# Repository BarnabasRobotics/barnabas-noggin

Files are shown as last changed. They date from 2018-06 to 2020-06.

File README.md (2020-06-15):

# barnabas-noggin
Controller board for Barnabas-Bot.  Arduino-Uno compatible board.  

Versions:
 
 Using Nano plug-in board
 - V3: Rev 2C 
 - V3.1: Rev 2D, Rev 2E
 
 No nano plug-in board
 - V4: Rev 3A, 3B 

Changes in Rev2D:
 - Remove 5V regulator
 - Add fuse protection on 5V and 3.3V
 - Add DC Driver Controller
 - Fix silkscreen text

Changes in Rev2E:
 - Silkscreen updates

[AutoDesk Fusion 360 file](https://a360.co/3gs5b8a)

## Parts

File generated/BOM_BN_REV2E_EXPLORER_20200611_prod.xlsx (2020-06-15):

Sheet: Barnabas Noggin rev 2D
ITEM | PART ID | VALUE | PACKAGE | SPECIFICATION | QTY | NOTES | BRAND | DIGIKEY PART # | MFG PART # | Notes
1 | C1 | 1uF | 603 | C0603-ROUND | 1 |  | Yageo | 311-1445-2-ND | CC0603KRX5R8BB105 | Substitute is OK
2 | J5, J7, J8 | 2.54mm | Thru-Hole | 2.54 mm female 1 x 6 | 3 |  | Harwin Inc. | 952-1809-ND | M20-7820646 | Substitute is OK
3 | J6, J9 | 2.54mm | Thru-Hole | 2.54 mm female 1 x 8 | 2 |  | Sullins Connector Solutions | S7006-ND | PPTC081LFBN-RC | Substitute is OK
4 | C2, C3, C4, C5 | 100nF | 603 | C0603-ROUND | 4 |  | Yageo | 311-1343-2-ND | CC0603ZRY5V9BB104 | Substitute is OK
5 | R1, R2, E2 | 2.54mm | Thru-Hole | 1x 1 Pin Female Header | 6 | 1 pin per hole | PE Connectors | NA | HWS6903 | Substitute is OK
6 | Nano | 2.54mm | Thru-Hole | 2.54 mm female 1 x 15 | 2 |  | Sullins Connector Solutions | S7013-ND | ber PPTC151LFBN-RC | Substitute is OK
7 | F1, F2 | FUSE_6V | 603 | FUSE_0603 | 2 |  | Bourns Inc. | MF-FSMF050X-2CT-ND | MF-FSMF050X-2 | Substitute is OK
8 | J3, J4 | 2.54mm | Thru-Hole | 2.54 mm header 2 x 3 | 2 |  | Harwin Inc. | 952-2121-ND | M20-9980346 | Substitute is OK
9 | E1 | 2.54mm | Thru-Hole | 2.54 mm header 1 x 2 | 1 |  | PE Connectors | NA | hws5160 | Substitute is OK
10 | J1 | POWER_JACKPTH | Thru-Hole | POWER_JACK_PTH | 1 |  | MPD (Memory Protection Devices) | EJ508A-ND | EJ508A | Substitute is OK
11 | D1 | SS1P3L | DO-220AA | DIODI_DO220AAL | 1 |  | Vishay Semiconductor Diodes Division | SS1P3L-M3/84AGITR-ND | SS1P3L-M3/84A | Substitute is OK
 |  |  |  | Total Thru Hole | 17
 |  |  |  | Total SMD | 8
 |  |  |  | Total parts | 25

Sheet: Revision History
Date
2020-06-11 | Added LED header

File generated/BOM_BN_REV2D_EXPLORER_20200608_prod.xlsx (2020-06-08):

ITEM | PART ID | VALUE | PACKAGE | SPECIFICATION | QTY | NOTES | BRAND | DIGIKEY PART # | MFG PART # | Notes
1 | C1 | 1uF | 603 | C0603-ROUND | 1 |  | Yageo | 311-1445-2-ND | CC0603KRX5R8BB105
2 | J5, J7, J8 | 2.54mm | Thru-Hole | 2.54 mm female 1 x 6 | 3 |  | Harwin Inc. | 952-1809-ND | M20-7820646
3 | J6, J9 | 2.54mm | Thru-Hole | 2.54 mm female 1 x 8 | 2 |  | Sullins Connector Solutions | S7006-ND | PPTC081LFBN-RC
5 | C2, C3, C4, C5 | 100nF | 603 | C0603-ROUND | 4 |  | Yageo | 311-1343-2-ND | CC0603ZRY5V9BB104
6 | R1, R2 | 470 | Thru-Hole | RESISTOR_PTH | 2 | NO PLACE | * | * | * | NO PLACE
7 | Nano | 2.54mm | Thru-Hole | 2.54 mm female 1 x 15 | 2 |  | Sullins Connector Solutions | S7013-ND | ber PPTC151LFBN-RC
8 | E2 | BUZZER | Thru-Hole | 5V Passive buzzer | 1 | NO PLACE | * | * | * | NO PLACE
9 | F1, F2 | FUSE_6V | 603 | FUSE_0603 | 2 |  | Bourns Inc. | MF-FSMF050X-2CT-ND | MF-FSMF050X-2
10 | J3, J4 | 2.54mm | Thru-Hole | 2.54 mm header 2 x 3 | 2 |  | Harwin Inc. | 952-2121-ND | M20-9980346
11 | E1 | 5mm | Thru-Hole | LED5MM | 1 | NO PLACE | * | * | * | NO PLACE
12 | J1 | POWER_JACKPTH | Thru-Hole | POWER_JACK_PTH | 1 |  | MPD (Memory Protection Devices) | EJ508A-ND | EJ508A
13 | D1 | SS1P3L | DO-220AA | DIODI_DO220AAL | 1 |  | Vishay Semiconductor Diodes Division | SS1P3L-M3/84AGITR-ND | SS1P3L-M3/84A
 |  |  |  | Total Thru Hole | 14
 |  |  |  | Total SMD | 8
 |  |  |  | Total parts | 22

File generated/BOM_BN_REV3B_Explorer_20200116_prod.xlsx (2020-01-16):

ITEM | PART ID | VALUE | PACKAGE | SPECIFICATION | QTY | NOTES | BRAND | DIGIKEY PART # | MFG PART # | Notes
1 | R1, R4, R5, R6, R7, R8, R9 | 1K | 603 | RES SMD 1K OHM 1% 1/10W 0603 | 7 |  | Yageo | 311-1.00KHRTR-ND | RC0603FR-071KL
2 | C2, C4, C5, C6, C13 | 1uF | 603 | CAP CER 1UF 25V X5R 0603 | 5 |  | Yageo | 311-1445-2-ND | CC0603KRX5R8BB105
3 | J6, J7, J9 | 2.54mm | Thru-Hole | CONN RCPT 6POS 0.1 TIN PCB | 3 |  | Harwin Inc. | 952-1809-ND | M20-7820646
4 | J8, J10 | 2.54mm | Thru-Hole | CONN HDR 8POS 0.1 TIN PCB | 2 |  | Sullins Connector Solutions | S7006-ND | PPTC081LFBN-RC
5 | R2 | 4.7K | Thru-Hole | Thru-Hole Resistor | 1 | No Place | * | * | * | No Place
6 | C3, C10 | 4.7uF | 1206 | CAP CER 4.7UF 16V X5R 1206 | 2 |  | Samsung Electro-Mechanics | 1276-3059-2-ND | CL31A475KOHNNNE
7 | X2 | 12MHz | 3-SMD | CER RES 12.0000MHZ 33PF SMD | 1 |  | Murata Electronics North America | 490-17943-2-ND | CSTNE12M0G550000R0
8 | X1 | 16MHZ | 3-SMD | CER RES 16.0000MHZ 15PF SMD | 1 |  | Murata Electronics North America | 490-17948-2-ND | CSTNE16M0V530000R0
9 | C1, C7, C8, C9, C11, C12, C14, C15 | 100nF | 603 | CAP CER 0.1UF 50V Y5V 0603 | 8 |  | Yageo | 311-1343-2-ND | CC0603ZRY5V9BB104
10 | PB1, PB2 | 157SW | * | SWITCH TACTILE SPST-NO 0.05A 12V | 2 |  | C&K | CKN10506TR-ND | PTS820 J15M SMTR LFS
11 | R3 | 470 | Thru-Hole | Thru-Hole Resistor | 1 | No Place | * | * | * | No Place
12 | U2 | ATMEGA328P-AU | TQFP32-08 | IC MCU 8BIT 32KB FLASH 32TQFP | 1 |  | Microchip Technology | ATMEGA328P-AU-ND | ATMEGA328P-AU
13 | E2 | BUZZER | Thru-Hole | 5V Passive Buzzer | 1 | No Place | * | * | * | No Place
14 | U4 | CH340G | * | CH340G | 1 |  | * | * | *
15 | F1, F2, F3 | FUSE_6V | 603 | PTC RESET FUSE 6V 500MA 0603 | 3 |  | Bourns Inc. | MF-FSMF050X-2CT-ND | MF-FSMF050X-2
16 | LED1, LED4 | Green | 805 | LED GREEN CLEAR CHIP SMD | 2 |  | Lite-On Inc. | 160-1423-2-ND | LTST-C171GKT
17 | J2, J3, J5 | ICSP | Thru-Hole | CONN HEADER VERT 6POS 2.54MM | 3 |  | Harwin Inc. | 952-2121-ND | M20-9980346
18 | U5 | L9110S_DRIVER | * | DC Motor Driver | 1 | No Place | * | * | * | No Place
19 | E1 | LEDPTH | Thru-Hole | Thru-Hole 3V LED | 1 | No Place | * | * | * | No Place
20 | U1 | LM1117IMPX-5.0 | SOT-223-4 | IC REG LINEAR 5V 800MA SOT223-4 | 1 |  | Texas Instruments | LM1117IMPX-5.0/NOPBTR-ND | LM1117IMPX-5.0/NOPB
21 | U3 | LP2985-XXDBVR | SOT-23-5 | IC REG LINEAR 3.3V 150MA SOT23-5 | 1 |  | Texas Instruments | 296-18476-2-ND | LP2985-33DBVR
22 | J1 | POWER_JACKPTH | Thru-Hole | CONN PWR JACK 2.1X5.5MM SOLDER | 1 |  | MPD (Memory Protection Devices) | EJ508A-ND | EJ508A
23 | LED3 | Red | 805 | LED RED CLEAR SMD | 1 |  | Lite-On Inc. | 160-1415-2-ND | LTST-C170KRKT
24 | D1, D2, D3 | SS1P3L | DO-220AA | DIODE SCHOTTKY 30V 1.5A DO220AA | 3 |  | Vishay Semiconductor Diodes Division | SS1P3L-M3/84AGITR-ND | SS1P3L-M3/84A
25 | J4 | USB-mini-90 -SMD | * | CONN RCPT USB2.0 MINI B SMD R/A | 1 |  | CUI Inc. | 102-4003-2-ND | UJ2-MBH-1-SMT-TR
26 | LED2 | Yellow | 805 | LED YELLOW CLEAR CHIP SMD | 1 |  | Lite-On Inc. | 160-1428-2-ND | LTST-C171KSKT
 | Total Thru Hole | 13
 | Total SMD | 42
 | Total Parts | 55

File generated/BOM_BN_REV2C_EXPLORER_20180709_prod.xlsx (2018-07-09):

ITEM | PART ID | VALUE | PACKAGE | SPECIFICATION | QTY | NOTES | BRAND | DIGIKEY PART # | MFG PART # | Notes | EBAY LINK
1 | BUZZER7 | 5V | Thru-Hole (12 mm) | 5V Active buzzer | 0 | NO PLACE |  |  |  | NO PLACE
2 | C1, C2, C3, C4, C5, C6 | 100 nF | 1206 | 100 nF SMD | 6 |  | Kemet | 399-1249-2-ND | C1206C104K5RAC7867 |  | http://www.ebay.com/itm/291539757911
3 | D1 | 1A 400V | Thru-Hole (DO41-10) | 1N4004 Diode | 1 |  | Diodes Incorporated | 1N4004DITR-ND | 1N4004-T |  | http://www.ebay.com/itm/141976942383
4 | VR1 | 5V | SOT223 | AMS1117-5.0 | 0 | NO PLACE | Advanced Monolithic Systems |  | AMS1117-5.0 |  | http://www.ebay.com/itm/361426721949
5 | 7-12V | NA | Thru-Hole | 2.1 mm DC connector | 1 |  | MPD (Memory Protection Devices) | EJ508A-ND | EJ508A |  | http://www.ebay.com/itm/261471107446
6 | 01234567, 8910111213GNDREF | 2.54mm | Thru-Hole | 2.54 mm female 1 x 8 | 2 |  | Sullins Connector Solutions | S7006-ND | PPTC081LFBN-RC |  | http://www.ebay.com/itm/171015694191
7 | VINGNDGND5V3.3VRST, A5A4A3A2A1A0 | 2.54mm | Thru-Hole | 2.54 mm female 1 x 6 | 2 |  | Harwin Inc. | 952-1809-ND | M20-7820646 |  | http://www.ebay.com/itm/171015694317
8 | SERVO3SERVO9, SERVO10SERVO11 | 2.54mm | Thru-Hole | 2.54 mm header 2 x 3 | 2 |  | Harwin Inc. | 952-2121-ND | M20-9980346 |  | http://www.ebay.com/itm/500pc-Gold-plated-Double-Rows-2x3-pins-2-54mm-H-11-6mm-Male-Pin-Header-RoHS-/130544119410
9 | LED7 | 5mm | Thru-Hole | 3V LED 5mm diameter | 0 | NO PLACE |  |  |  | NO PLACE
10 | R1, R2 | 470 Ohm | Thru-Hole | Resistor | 0 | NO PLACE |  |  |  | NO PLACE
11 | NANO | 2.54mm | Thru-Hole | 2.54 mm female 1 x 15 | 2 |  | Sullins Connector Solutions | S7013-ND | ber PPTC151LFBN-RC
 |  |  |  | Total Thru Hole | 10
 |  |  |  | Total SMD | 6
 |  |  |  | Total parts | 16

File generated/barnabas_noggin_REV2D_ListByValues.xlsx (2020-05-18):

Qty | Value | Part Num | Package | Parts | Mfg Name | VID | Vendor Part Num | Description | Pkg Code | XREF
1 | 1uF | CC0603KRX5R8BB105 | C0603-ROUND | C1 | Yageo | DK | 311-1445-2-ND | CAP CER 1UF 25V X5R 0603 | 603 | REF9
3 | 2.54mm | M20-7820646 | 1X06 | J5, J7, J8 | Harwin Inc. | DK | 952-1809-ND | CONN RCPT 6POS 0.1 TIN PCB | REF19 | *
2 | 2.54mm | PPTC081LFBN-RC | 1X08 | J6, J9 | Sullins Connector Solutions | DK | S7006-ND | CONN HDR 8POS 0.1 TIN PCB | REF18 | *
1 | 4.7K | * | RESISTOR_PTH | R1 | * | * | * | * | * | *
4 | 100nF | CC0603ZRY5V9BB104 | C0603-ROUND | C2, C3, C4, C5 | Yageo | DK | 311-1343-2-ND | CAP CER 0.1UF 50V Y5V 0603 | 603 | REF10
1 | 470 | * | RESISTOR_PTH | R2 | * | * | * | * | * | *
1 | ARDUINONANO | * | PDIP-32 | U$1 | * | * | * | * | * | *
1 | BUZZER | * | BUZZER | E2 | * | * | * | * | * | *
2 | FUSE_6V | MF-FSMF050X-2 | FUSE_0603 | F1, F2 | Bourns Inc. | DK | MF-FSMF050X-2CT-ND | PTC RESET FUSE 6V 500MA 0603 | 603 | REF1
2 | ICSP | M20-9980346 | CONNECTOR_2X3 | J3, J4 | Harwin Inc. | DK | 952-2121-ND | CONN HEADER VERT 6POS 2.54MM | * | REF20
1 | L9110S_DRIVER | * | L9110S_DRIVER | U1 | * | * | * | * | * | *
1 | LEDPTH | * | LED5MM | E1 | * | * | * | * | * | *
1 | POWER_JACKPTH | EJ508A | POWER_JACK_PTH | J1 | MPD (Memory Protection Devices) | DK | EJ508A-ND | CONN PWR JACK 2.1X5.5MM SOLDER | * | REF17
1 | SS1P3L | SS1P3L-M3/84A | DIODI_DO220AAL | D1 | Vishay Semiconductor Diodes Division | DK | SS1P3L-M3/84AGITR-ND | DIODE SCHOTTKY 30V 1.5A DO220AA | DO-220AA | REF5

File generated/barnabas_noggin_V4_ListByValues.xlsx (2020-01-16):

Qty | Value | Part Num | Package | Parts | Mfg Name | VID | Vendor Part Num | Description | Pkg Code | XREF
7 | 1K | RC0603FR-071KL | R0603 | R1, R4, R5, R6, R7, R8, R9 | Yageo | DK | 311-1.00KHRTR-ND | RES SMD 1K OHM 1% 1/10W 0603 | 603 | REF7
5 | 1uF | CC0603KRX5R8BB105 | C0603-ROUND | C2, C4, C5, C6, C13 | Yageo | DK | 311-1445-2-ND | CAP CER 1UF 25V X5R 0603 | 603 | REF9
3 | 2.54mm | M20-7820646 | 1X06 | J6, J7, J9 | Harwin Inc. | DK | 952-1809-ND | CONN RCPT 6POS 0.1 TIN PCB | REF19 | *
2 | 2.54mm | PPTC081LFBN-RC | 1X08 | J8, J10 | Sullins Connector Solutions | DK | S7006-ND | CONN HDR 8POS 0.1 TIN PCB | REF18 | *
1 | 4.7K | * | RESISTOR_PTH | R2 | * | * | * | * | * | *
2 | 4.7uF | CL31A475KOHNNNE | TAN-A | C3, C10 | Samsung Electro-Mechanics | DK | 1276-3059-2-ND | CAP CER 4.7UF 16V X5R 1206 | 1206 | REF11
1 | 12MHz | CSTNE12M0G550000R0 | CRYSTAL | X2 | Murata Electronics North America | DK | 490-17943-2-ND | CER RES 12.0000MHZ 33PF SMD | 3-SMD | REF4
1 | 16MHZ | CSTNE16M0V530000R0 | CRYSTAL | X1 | Murata Electronics North America | DK | 490-17948-2-ND | CER RES 16.0000MHZ 15PF SMD | 3-SMD | REF3
8 | 100nF | CC0603ZRY5V9BB104 | C0603-ROUND | C1, C7, C8, C9, C11, C12, C14, C15 | Yageo | DK | 311-1343-2-ND | CAP CER 0.1UF 50V Y5V 0603 | 603 | REF10
2 | 157SW | PTS820 J15M SMTR LFS | SWITCHES_SMD_157SW | PB1, PB2 | C&K | DK | CKN10506TR-ND | SWITCH TACTILE SPST-NO 0.05A 12V | REF23 | *
1 | 470 | * | RESISTOR_PTH | R3 | * | * | * | * | * | *
1 | ATMEGA328P-AU | ATMEGA328P-AU | TQFP32-08 | U2 | Microchip Technology | DK | ATMEGA328P-AU-ND | IC MCU 8BIT 32KB FLASH 32TQFP | 32-TQFP | REF2
1 | BUZZER | * | BUZZER | E2 | * | * | * | * | * | *
1 | CH340G | * | SOIC16 | U4 | * | * | * | * | * | *
3 | FUSE_6V | MF-FSMF050X-2 | FUSE_0603 | F1, F2, F3 | Bourns Inc. | DK | MF-FSMF050X-2CT-ND | PTC RESET FUSE 6V 500MA 0603 | 603 | REF1
2 | Green | LTST-C171GKT | LED_0805 | LED1, LED4 | Lite-On Inc. | DK | 160-1423-2-ND | LED GREEN CLEAR CHIP SMD | 805 | REF12
3 | ICSP | M20-9980346 | CONNECTOR_2X3 | J2, J3, J5 | Harwin Inc. | DK | 952-2121-ND | CONN HEADER VERT 6POS 2.54MM | * | REF20
1 | L9110S_DRIVER | * | L9110S_DRIVER | U5 | * | * | * | * | * | *
1 | LEDPTH | * | LED5MM | E1 | * | * | * | * | * | *
1 | LM1117IMPX-5.0 | LM1117IMPX-5.0/NOPB | LM1117_SOT223 | U1 | Texas Instruments | DK | LM1117IMPX-5.0/NOPBTR-ND | IC REG LINEAR 5V 800MA SOT223-4 | SOT-223-4 | REF6
1 | LP2985-XXDBVR | LP2985-33DBVR | SOT23-DBV | U3 | Texas Instruments | DK | 296-18476-2-ND | IC REG LINEAR 3.3V 150MA SOT23-5 | SOT-23-5 | REF22
4 | MOUNT_HOLE | * | MOUNT_HOLE | M1, M2, M3, M4 | * | * | * | * | * | *
1 | POWER_JACKPTH | EJ508A | POWER_JACK_PTH | J1 | MPD (Memory Protection Devices) | DK | EJ508A-ND | CONN PWR JACK 2.1X5.5MM SOLDER | * | REF17
1 | Red | LTST-C170KRKT | LED_0805 | LED3 | Lite-On Inc. | DK | 160-1415-2-ND | LED RED CLEAR SMD | 805 | REF13
3 | SS1P3L | SS1P3L-M3/84A | DIODI_DO220AAL | D1, D2, D3 | Vishay Semiconductor Diodes Division | DK | SS1P3L-M3/84AGITR-ND | DIODE SCHOTTKY 30V 1.5A DO220AA | DO-220AA | REF5
1 | USB-mini-90 -SMD | UJ2-MBH-1-SMT-TR | CONNECTOR_USB_MINI-B | J4 | CUI Inc. | DK | 102-4003-2-ND | CONN RCPT USB2.0 MINI B SMD R/A | * | REF21
1 | Yellow | LTST-C171KSKT | LED_0805 | LED2 | Lite-On Inc. | DK | 160-1428-2-ND | LED YELLOW CLEAR CHIP SMD | 805 | REF14

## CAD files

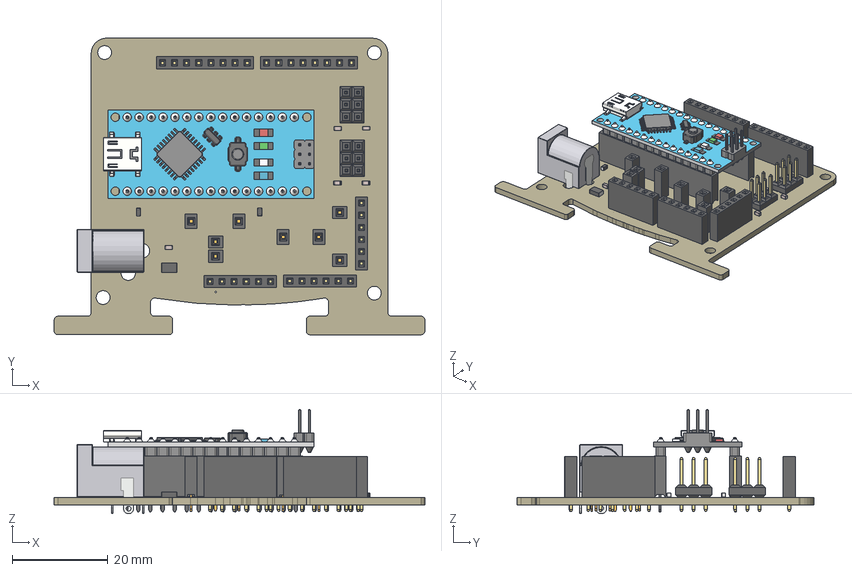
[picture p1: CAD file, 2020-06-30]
generated/barnabas_noggin_Rev2E.step
77.7 x 62.1 x 21.9 mm
1X06 x 3
1X08 x 2
C0603-ROUND x 5
CONNECTOR_2X3 x 2
DIODI_DO220AAL
FUSE_0603 x 2
L9110S_DRIVER
POWER_JACK_PTH
arduio nano
ZL262-1S_P2-54_L2-54_W2-54_H8-5 x 2
ZL262-1S_P2-54_L2-54_W2-54_H8-5 (1) x 2
ZL262-1S_P2-54_L2-54_W2-54_H8-5 (2) x 4

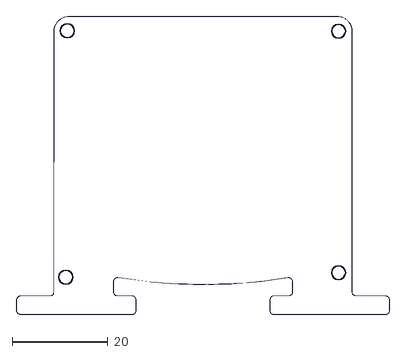
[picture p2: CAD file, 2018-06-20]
pcb-outline/schematic_V3_mm_2_r14 version.dxf
77.8 x 62.2

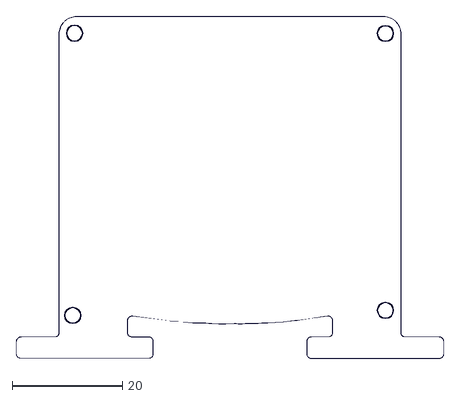
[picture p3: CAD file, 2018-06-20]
pcb-outline/schematic_V3_mm.dxf
77.8 x 62.2

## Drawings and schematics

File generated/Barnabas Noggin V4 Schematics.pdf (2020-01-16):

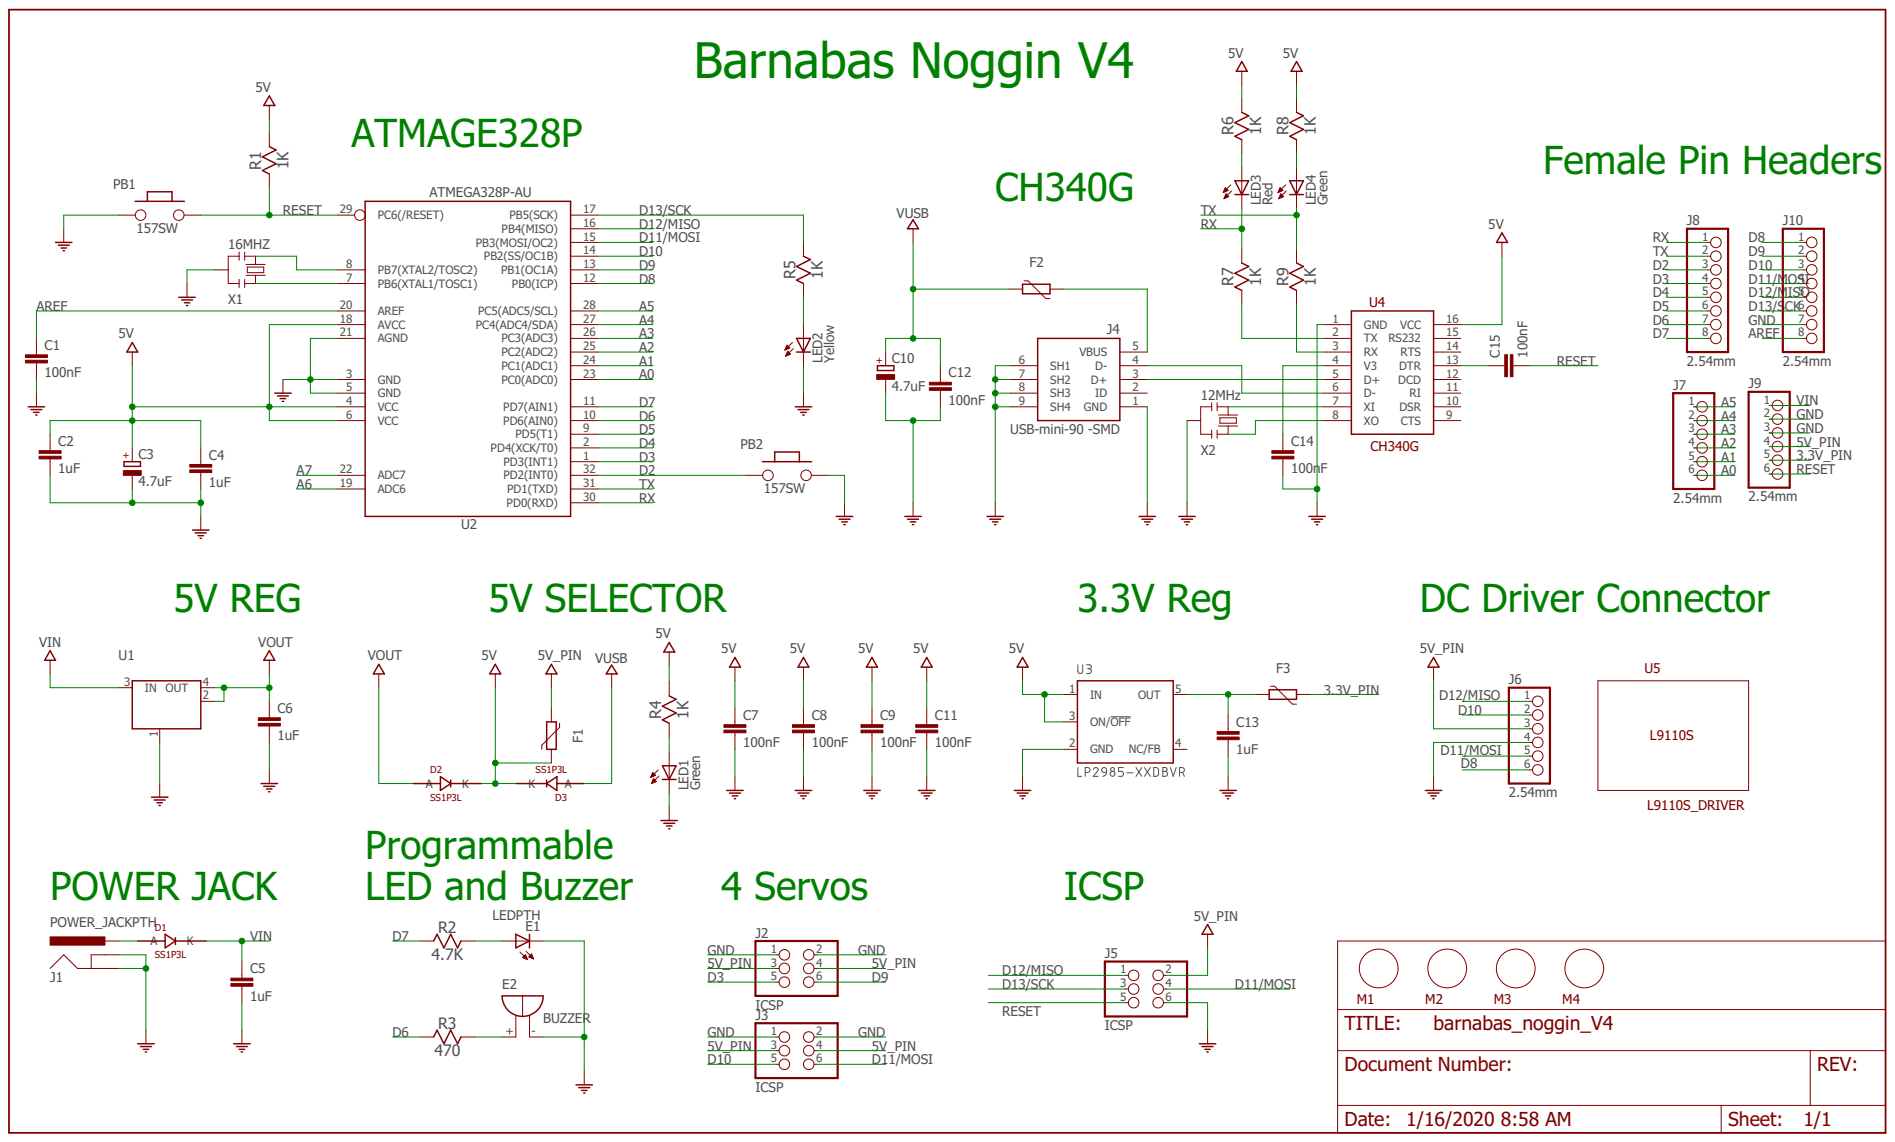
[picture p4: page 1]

REV: TITLE: Document Number: barnabas_noggin_V4

Date: 1/16/2020 8:58 AM | Sheet: 1/1

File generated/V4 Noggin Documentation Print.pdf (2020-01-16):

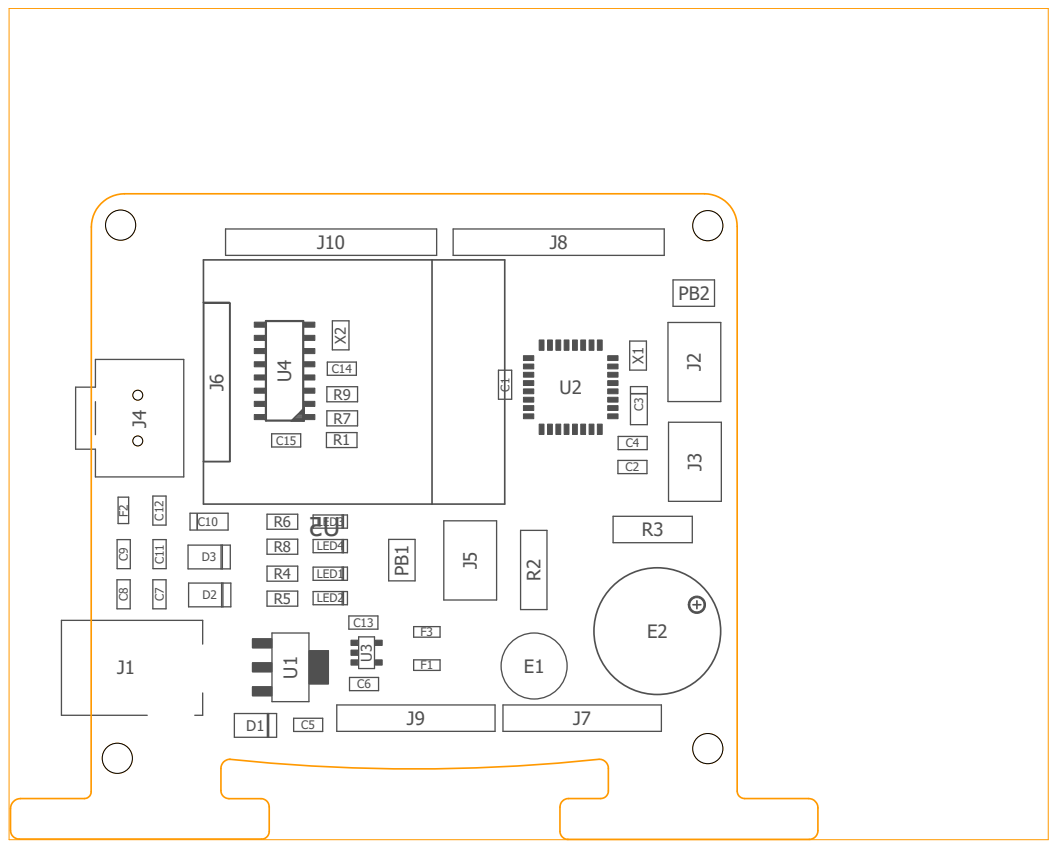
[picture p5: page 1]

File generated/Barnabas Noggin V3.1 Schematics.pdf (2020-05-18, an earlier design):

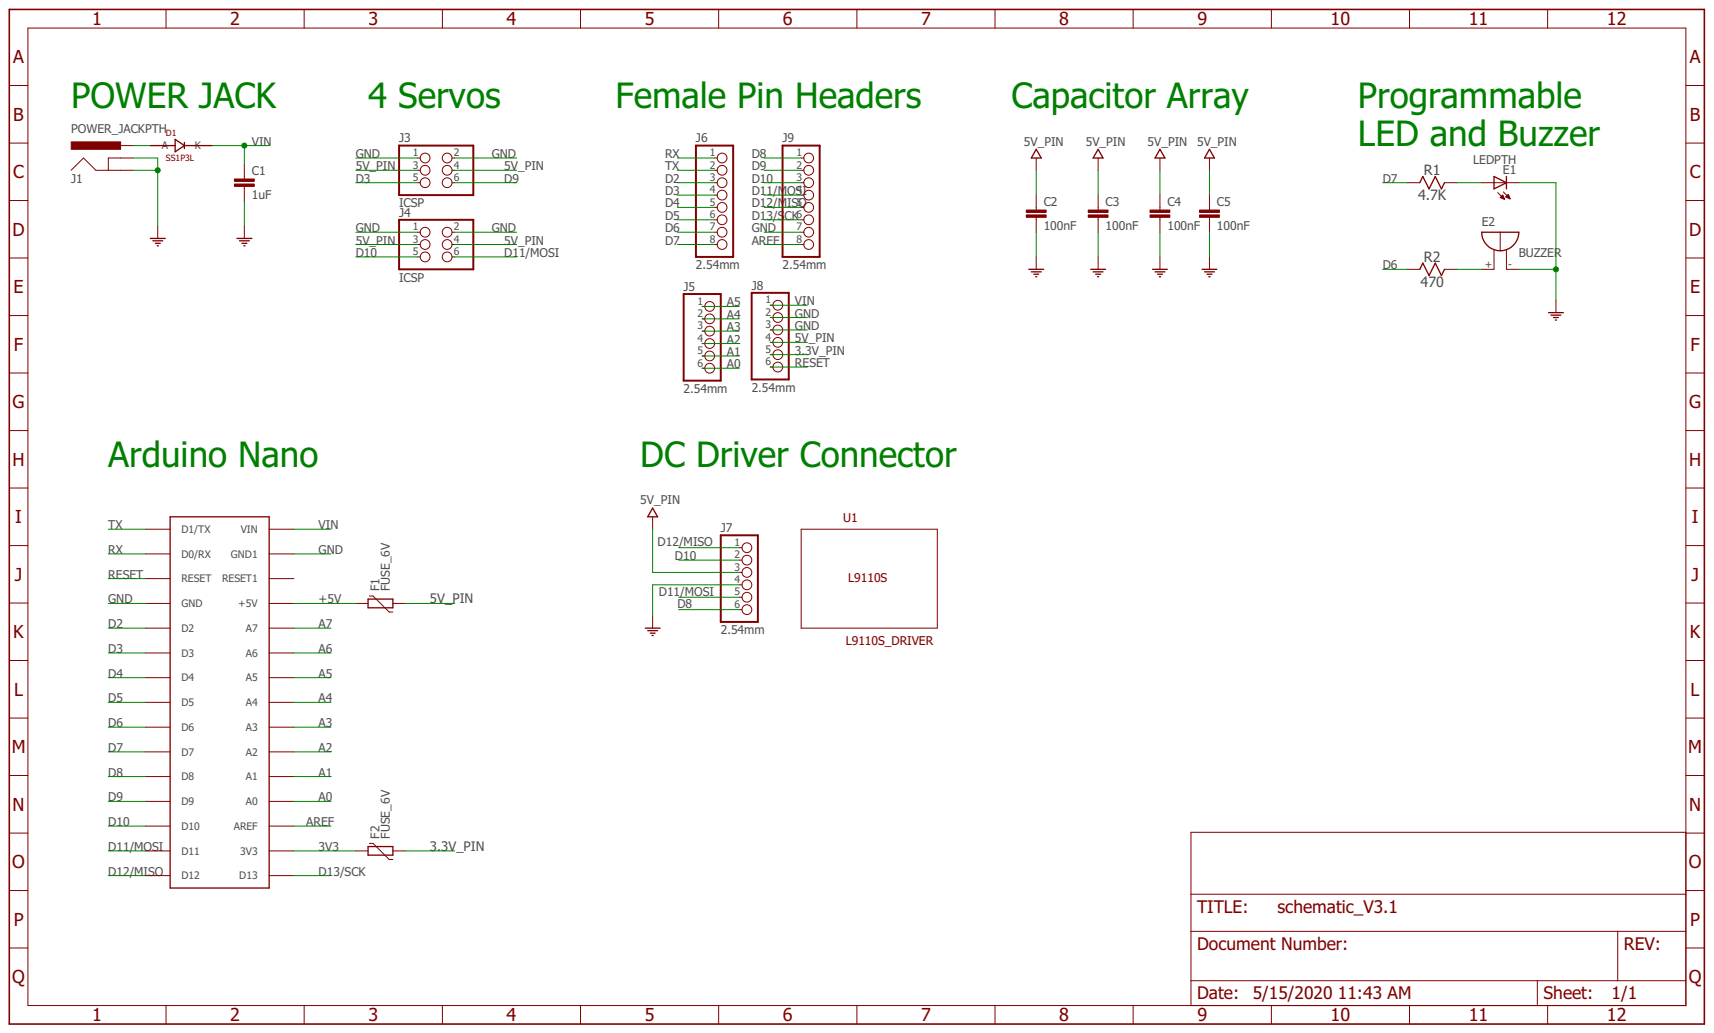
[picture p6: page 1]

REV: TITLE: Document Number: schematic_V3.1

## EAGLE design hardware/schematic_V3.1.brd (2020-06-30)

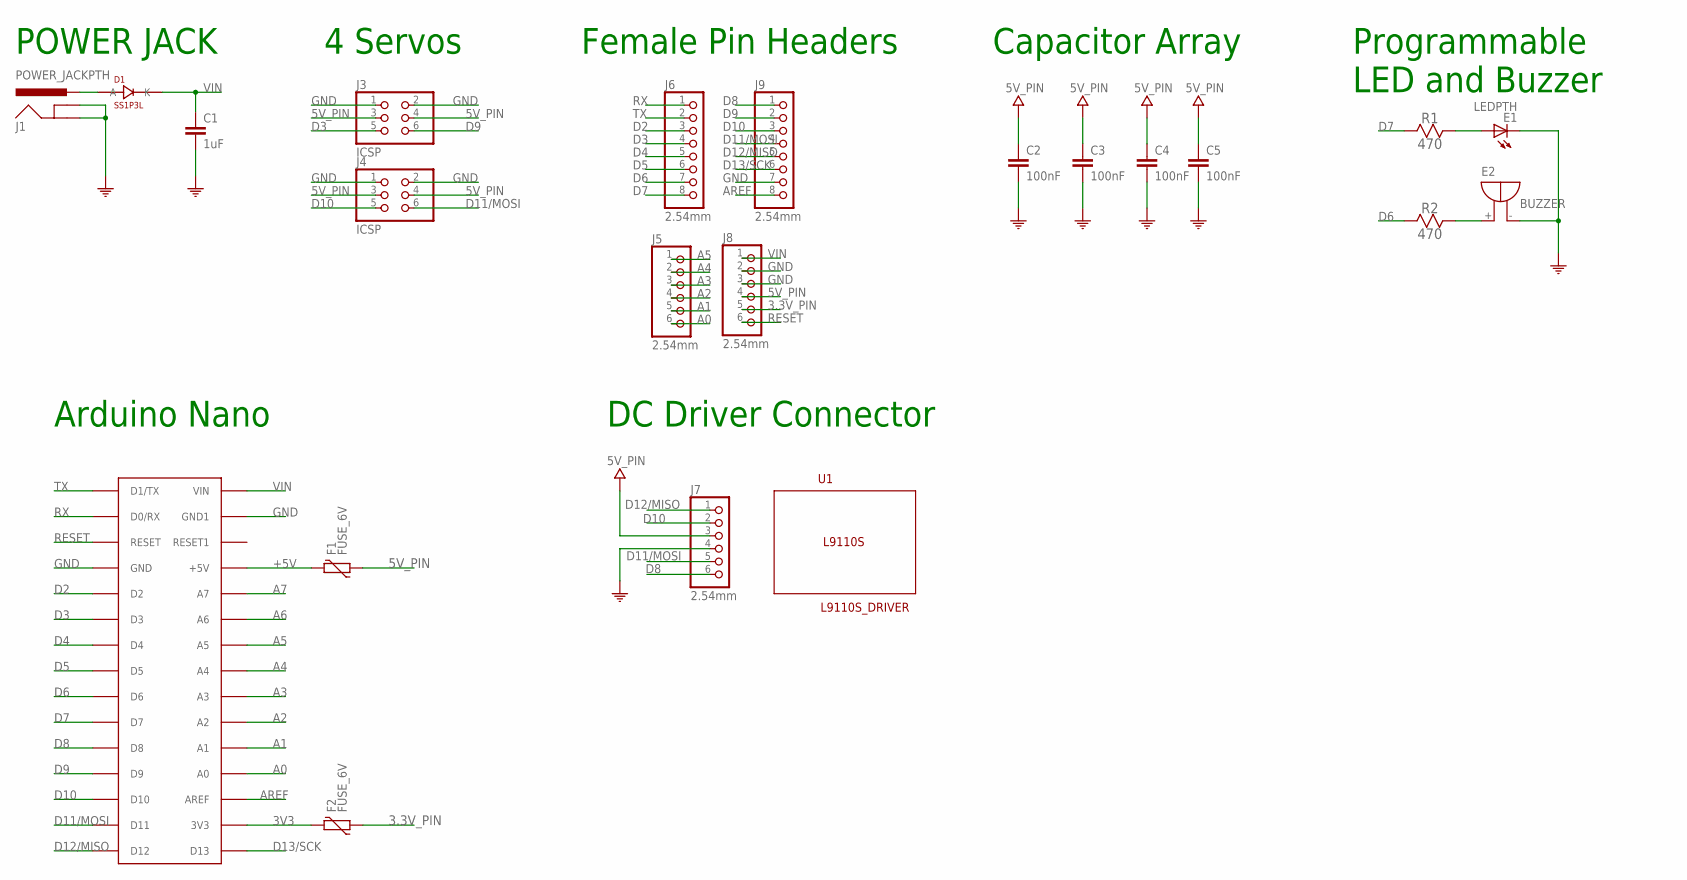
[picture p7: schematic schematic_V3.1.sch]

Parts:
C1: 1uF; C0603-ROUND; PARTNO CC0603KRX5R8BB105
C2, C3, C4, C5: 100nF; C0603-ROUND; PARTNO CC0603ZRY5V9BB104
D1: SS1P3L; DIODI_DO220AAL; PARTNO SS1P3L-M3/84A
E1: LEDPTH; LED5MM
E2: BUZZER
F1, F2: FUSE_6V; FUSE_0603; PARTNO MF-FSMF050X-2
J1: POWER_JACKPTH; POWER_JACK_PTH; PARTNO EJ508A
J3, J4: ICSP; CONNECTOR_2X3; PARTNO M20-9980346
J5, J7, J8: 2.54mm; 1X06; PARTNO M20-7820646
J6, J9: 2.54mm; 1X08; PARTNO PPTC081LFBN-RC
R1, R2: 470; RESISTOR_PTH
U1: L9110S_DRIVER
U$1: ARDUINONANO; PDIP-32

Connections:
3.3V_PIN: F2.1, J8.5
3V3: F2.2, U$1.3V3
5V_PIN: C2.1, C3.1, C4.1, C5.1, F1.1, J3.3, J3.4, J4.3, J4.4, J7.3, J8.4
+5V: F1.2, U$1.+5V
A0: J5.6, U$1.A7 (A0)
A1: J5.5, U$1.A6 (A1)
A2: J5.4, U$1.A5 (A2)
A3: J5.3, U$1.A4 (A3)
A4: J5.2, U$1.A3 (A4)
A5: J5.1, U$1.A2 (A5)
A6: U$1.A1 (A6)
A7: U$1.A0 (A7)
AREF: J9.8, U$1.AREF
D2: J6.3, U$1.D2
D3: J3.5, J6.4, U$1.D3
D4: J6.5, U$1.D4
D5: J6.6, U$1.D5
D6: J6.7, R2.1, U$1.D6
D7: J6.8, R1.1, U$1.D7
D8: J7.6, J9.1, U$1.D8
D9: J3.6, J9.2, U$1.D9
D10: J4.5, J7.2, J9.3, U$1.D10
D11/MOSI: J4.6, J7.5, J9.4, U$1.D11
D12/MISO: J7.1, J9.5, U$1.D12
D13/SCK: J9.6, U$1.D13
GND: C1.2, C2.2, C3.2, C4.2, C5.2, E1.K (C), E2.-, J1.GND, J1.GNDBREAK, J3.1, J3.2, J4.1, J4.2, J7.4, J8.2, J8.3, J9.7, U$1.GND, U$1.GND1
unnamed: D1.P$2 (A), J1.PWR
unnamed: E1.A, R1.2
unnamed: E2.+, R2.2
RESET: J8.6, U$1.RESET
RX: J6.1, U$1.D0/RX
TX: J6.2, U$1.D1/TX
VIN: C1.1, D1.P$1 (K), J8.1, U$1.VIN

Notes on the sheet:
Arduino Nano
POWER JACK
4 Servos
Female Pin Headers
Programmable LED and Buzzer
Capacitor Array
DC Driver Connector

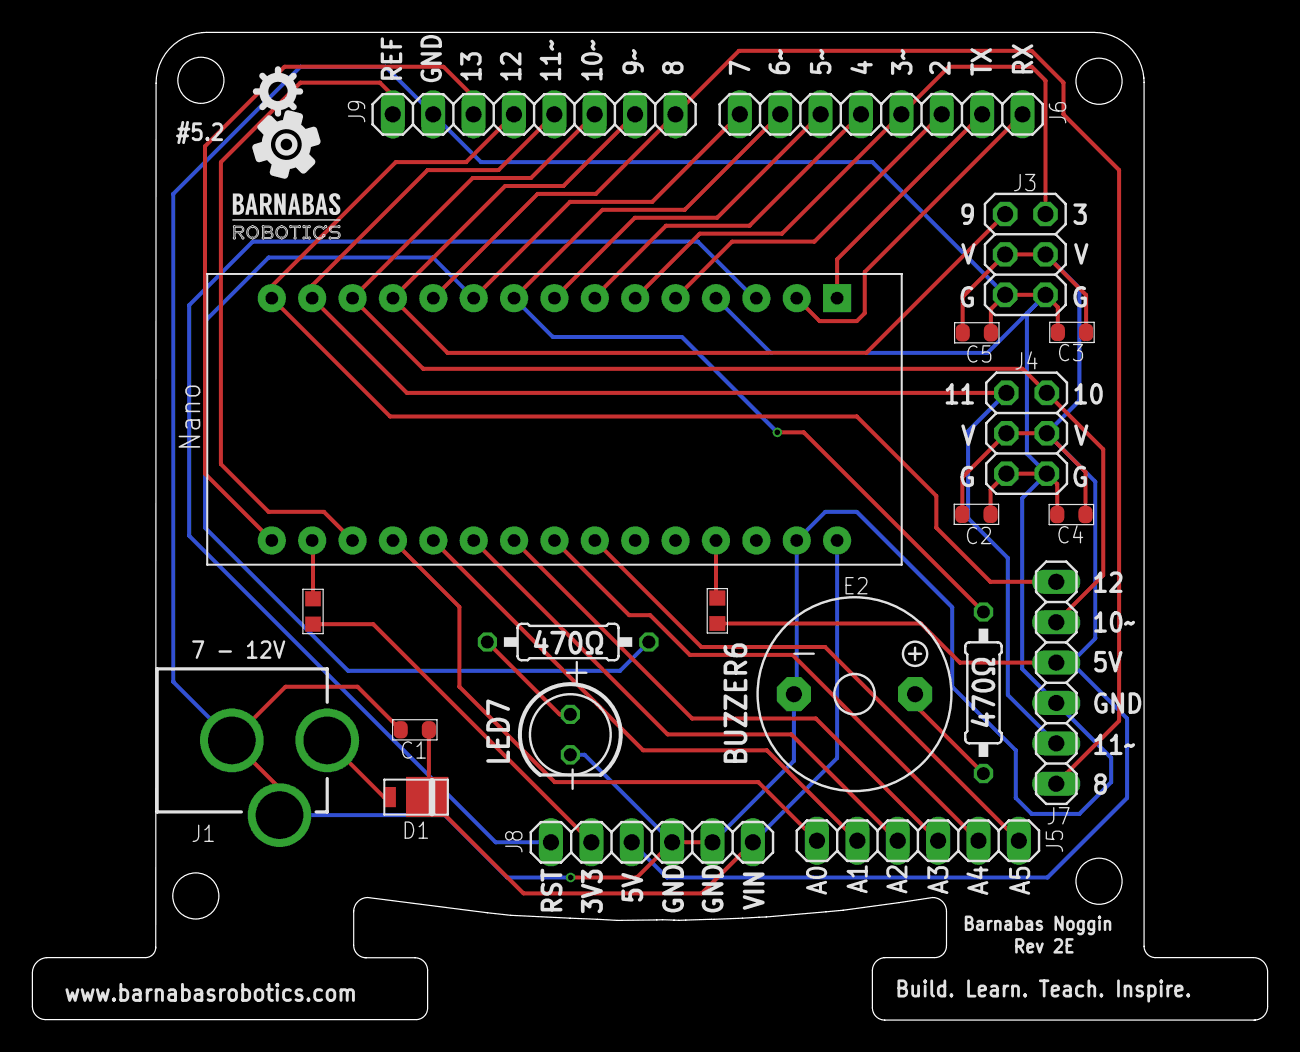
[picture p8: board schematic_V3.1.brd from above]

Board: 2 copper layers, 77.7 x 62.1 mm, 22 parts (0 on the bottom side), 31 nets.

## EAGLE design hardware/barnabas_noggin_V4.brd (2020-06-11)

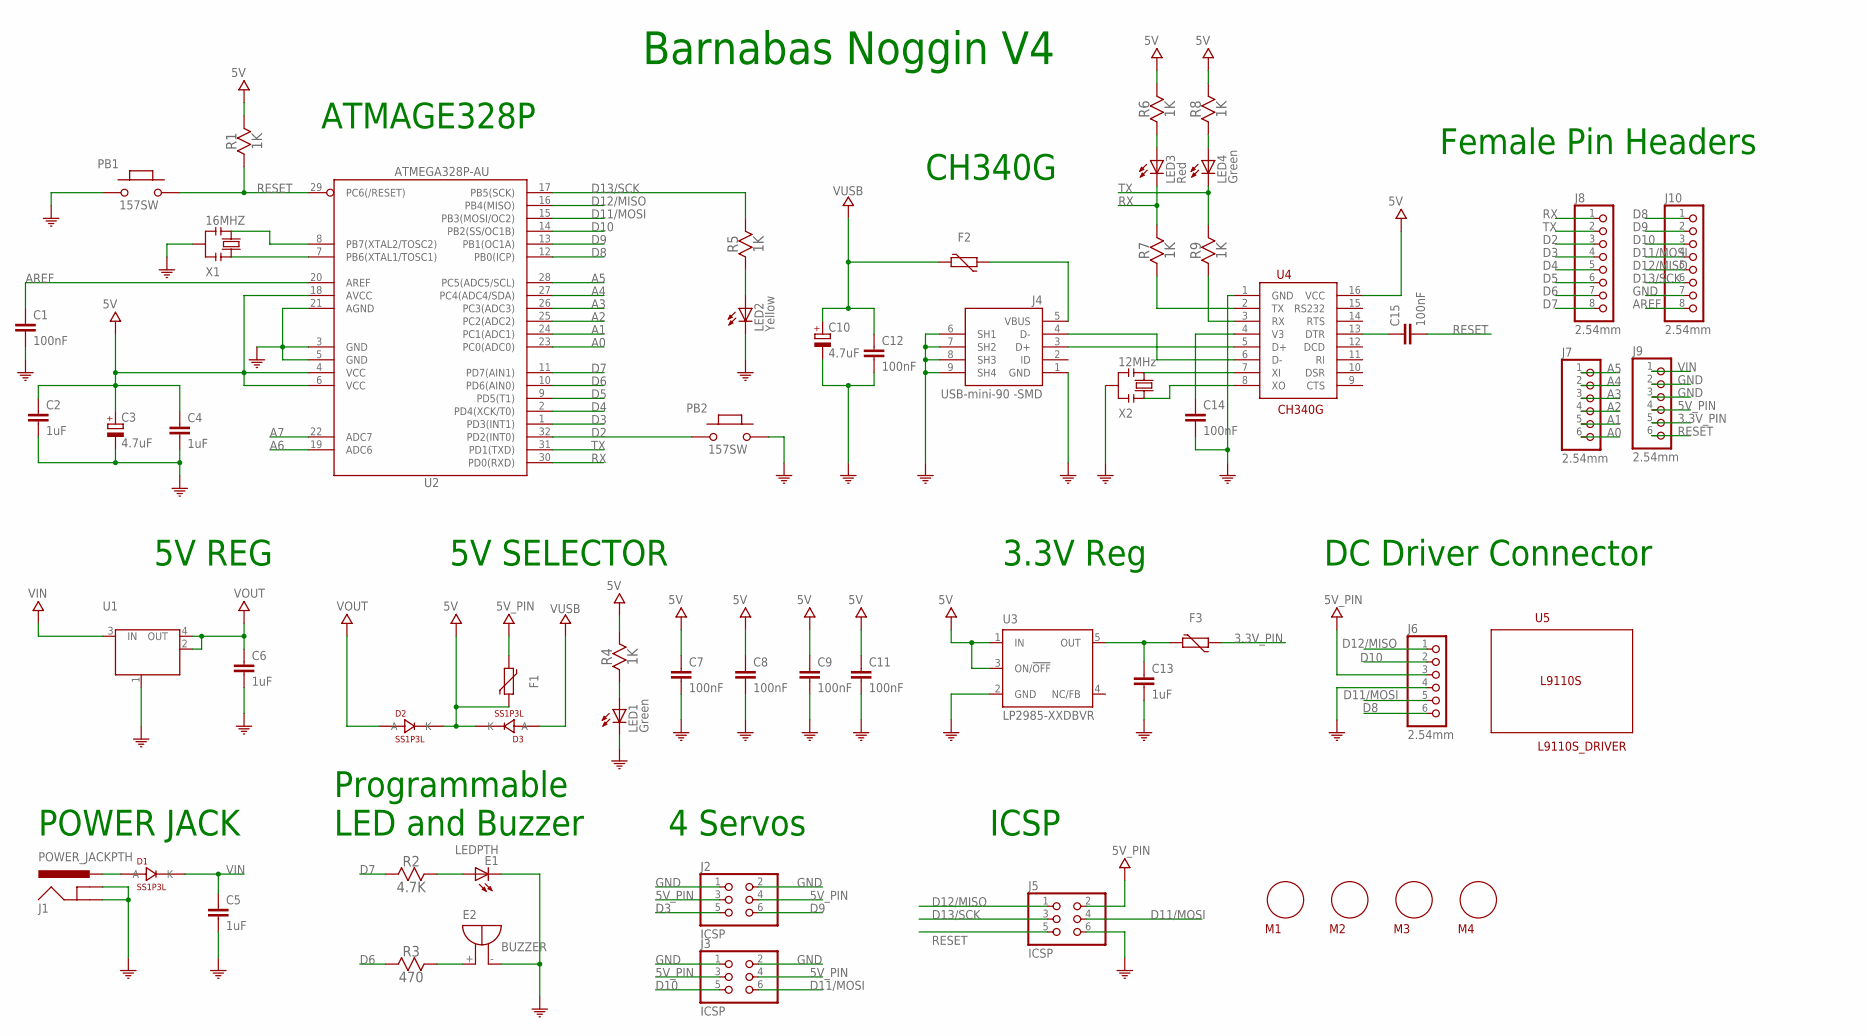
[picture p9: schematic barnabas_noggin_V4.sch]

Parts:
C1, C7, C8, C9, C11, C12, C14, C15: 100nF; C0603-ROUND; PARTNO CC0603ZRY5V9BB104
C2, C4, C5, C6, C13: 1uF; C0603-ROUND; PARTNO CC0603KRX5R8BB105
C3, C10: 4.7uF; TAN-A; PARTNO CL31A475KOHNNNE
D1, D2, D3: SS1P3L; DIODI_DO220AAL; PARTNO SS1P3L-M3/84A
E1: LEDPTH; LED5MM
E2: BUZZER
F1, F2, F3: FUSE_6V; FUSE_0603; PARTNO MF-FSMF050X-2
J1: POWER_JACKPTH; POWER_JACK_PTH; PARTNO EJ508A
J2, J3, J5: ICSP; CONNECTOR_2X3; PARTNO M20-9980346
J4: USB-mini-90 -SMD; CONNECTOR_USB_MINI-B; PARTNO UJ2-MBH-1-SMT-TR
J6, J7, J9: 2.54mm; 1X06; PARTNO M20-7820646
J8, J10: 2.54mm; 1X08; PARTNO PPTC081LFBN-RC
LED1, LED4: Green; LED_0805; PARTNO LTST-C171GKT
LED2: Yellow; LED_0805; PARTNO LTST-C171KSKT
LED3: Red; LED_0805; PARTNO LTST-C170KRKT
M1, M2, M3, M4: MOUNT_HOLE
PB1, PB2: 157SW; SWITCHES_SMD_157SW; PARTNO PTS820 J15M SMTR LFS
R1, R4, R5, R6, R7, R8, R9: 1K; R0603; PARTNO RC0603FR-071KL
R2: 4.7K; RESISTOR_PTH
R3: 470; RESISTOR_PTH
U1: LM1117IMPX-5.0; LM1117_SOT223; PARTNO LM1117IMPX-5.0/NOPB
U2: ATMEGA328P-AU; TQFP32-08; PARTNO ATMEGA328P-AU
U3: LP2985-XXDBVR; SOT23-DBV; PARTNO LP2985-33DBVR
U4: CH340G; SOIC16
U5: L9110S_DRIVER
X1: 16MHZ; CRYSTAL; PARTNO CSTNE16M0V530000R0
X2: 12MHz; CRYSTAL; PARTNO CSTNE12M0G550000R0

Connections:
3.3V: C13.1, F3.2, U3.5 (OUT)
3.3V_PIN: F3.1, J9.5
5V: C2.1, C3.1 (+), C4.1, C7.1, C8.1, C9.1, C11.1, D2.P$1 (K), D3.P$1 (K), F1.1, R1.2, R4.2, R6.2, R8.2, U2.4 (VCC), U2.6 (VCC), U2.18 (AVCC), U3.1 (IN), U3.3 (ON/!OFF), U4.16 (VCC)
5V_PIN: F1.2, J2.3, J2.4, J3.3, J3.4, J5.2, J6.3, J9.4
A0: J7.6, U2.23 (PC0(ADC0))
A1: J7.5, U2.24 (PC1(ADC1))
A2: J7.4, U2.25 (PC2(ADC2))
A3: J7.3, U2.26 (PC3(ADC3))
A4: J7.2, U2.27 (PC4(ADC4/SDA))
A5: J7.1, U2.28 (PC5(ADC5/SCL))
A6: U2.19 (ADC6)
A7: U2.22 (ADC7)
AREF: C1.1, J10.8, U2.20 (AREF)
D2: J8.3, PB2.1, U2.32 (PD2(INT0))
D3: J2.5, J8.4, U2.1 (PD3(INT1))
D4: J8.5, U2.2 (PD4(XCK/T0))
D5: J8.6, U2.9 (PD5(T1))
D6: J8.7, R3.1, U2.10 (PD6(AIN0))
D7: J8.8, R2.1, U2.11 (PD7(AIN1))
D8: J6.6, J10.1, U2.12 (PB0(ICP))
D9: J2.6, J10.2, U2.13 (PB1(OC1A))
D10: J3.5, J6.2, J10.3, U2.14 (PB2(SS/OC1B))
D11/MOSI: J3.6, J5.4, J6.5, J10.4, U2.15 (PB3(MOSI/OC2))
D12/MISO: J5.1, J6.1, J10.5, U2.16 (PB4(MISO))
D13/SCK: J5.3, J10.6, R5.2, U2.17 (PB5(SCK))
GND: C1.2, C2.2, C3.2 (-), C4.2, C5.2, C6.2, C7.2, C8.2, C9.2, C10.2 (-), C11.2, C12.2, C13.2, C14.2, E1.K (C), E2.-, J1.GND, J1.GNDBREAK, J2.1, J2.2, J3.1, J3.2, J4.1 (GND), J4.6 (SH1), J4.7 (SH2), J4.8 (SH3), J4.9 (SH4), J5.6, J6.4, J9.2, J9.3, J10.7, LED1.C, LED2.C, PB1.1, PB2.2, U1.1 (GND/ADJ), U2.3 (GND), U2.5 (GND), U2.21 (AGND), U3.2 (GND), U4.1 (GND), X1.2, X2.2
unnamed: U2.8 (PB7(XTAL2/TOSC2)), X1.3
unnamed: U2.7 (PB6(XTAL1/TOSC1)), X1.1
unnamed: LED1.A, R4.1
unnamed: C15.1, U4.13 (DTR)
unnamed: U4.7 (XI), X2.3
unnamed: R7.1, U4.2 (TX)
unnamed: LED3.A, R6.1
unnamed: R9.1, U4.3 (RX)
unnamed: LED4.A, R8.1
unnamed: LED2.A, R5.1
unnamed: C14.1, U4.4 (V3)
unnamed: U4.8 (XO), X2.1
unnamed: J4.3 (D+), U4.5 (D+)
unnamed: J4.4 (D-), U4.6 (D-)
unnamed: D1.P$2 (A), J1.PWR
unnamed: F2.1, J4.5 (VBUS)
unnamed: E1.A, R2.2
unnamed: E2.+, R3.2
RESET: C15.2, J5.5, J9.6, PB1.2, R1.1, U2.29 (PC6(/RESET))
RX: J8.1, LED3.C, R7.2, U2.30 (PD0(RXD))
TX: J8.2, LED4.C, R9.2, U2.31 (PD1(TXD))
VIN: C5.1, D1.P$1 (K), J9.1, U1.3 (IN)
VOUT: C6.1, D2.P$2 (A), U1.2 (OUT), U1.4 (OUT)
VUSB: C10.1 (+), C12.1, D3.P$2 (A), F2.2

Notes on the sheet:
Barnabas Noggin V4
5V REG
ICSP
5V SELECTOR
ATMAGE328P
CH340G
POWER JACK
Programmable LED and Buzzer
4 Servos
Female Pin Headers
DC Driver Connector
3.3V Reg

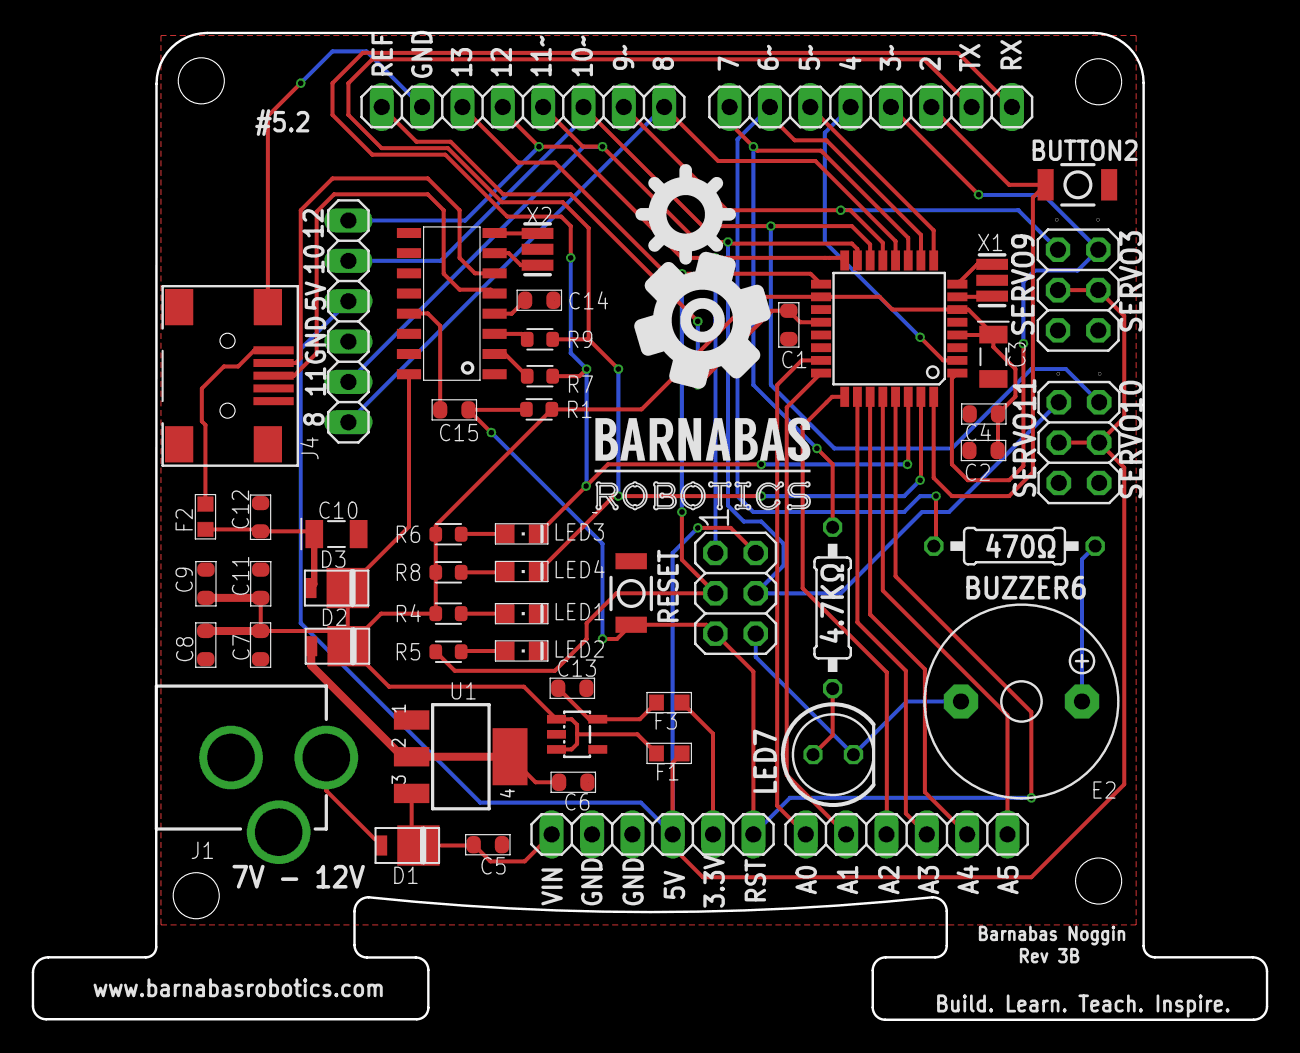
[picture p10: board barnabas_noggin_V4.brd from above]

Board: 2 copper layers, 77.7 x 62.1 mm, 60 parts (1 on the bottom side), 48 nets.

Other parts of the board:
U$14: BARNABAS_LOGO

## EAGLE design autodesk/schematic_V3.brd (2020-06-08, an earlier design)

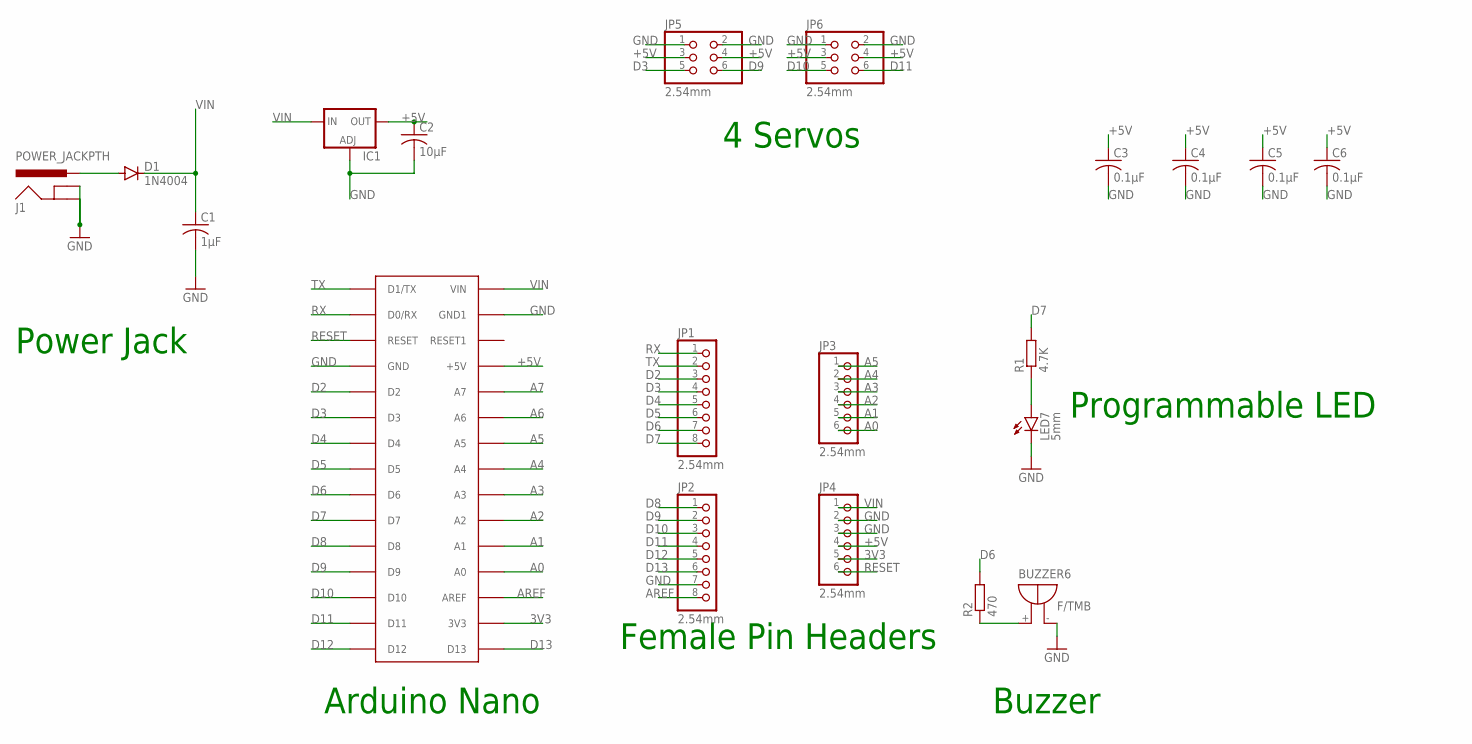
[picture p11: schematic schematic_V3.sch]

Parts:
BUZZER6: F/TMB
C1: 1μF; C1206
C2: 10μF; C1206
C3, C4, C5, C6: 0.1μF; C1206
D1: 1N4004; DO41-10
IC1: VR1; SOT223
J1: POWER_JACKPTH; POWER_JACK_PTH
JP1, JP2: 2.54mm; 1X08
JP3, JP4: 2.54mm; 1X06
JP5, JP6: 2.54mm; 2X03
LED7: 5mm; LED5MM
R1: 4.7K; 0207/10
R2: 470; 0207/10
U$1: ARDUINONANO; PDIP-32

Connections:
3V3: JP4.5, U$1.3V3
+5V: C2.1, C3.1, C4.1, C5.1, C6.1, IC1.4 (OUT), JP4.4, JP5.3, JP5.4, JP6.3, JP6.4, U$1.+5V
A0: JP3.6, U$1.A7 (A0)
A1: JP3.5, U$1.A6 (A1)
A2: JP3.4, U$1.A5 (A2)
A3: JP3.3, U$1.A4 (A3)
A4: JP3.2, U$1.A3 (A4)
A5: JP3.1, U$1.A2 (A5)
A6: U$1.A1 (A6)
A7: U$1.A0 (A7)
AREF: JP2.8, U$1.AREF
D2: JP1.3, U$1.D2
D3: JP1.4, JP5.5, U$1.D3
D4: JP1.5, U$1.D4
D5: JP1.6, U$1.D5
D6: JP1.7, R2.2, U$1.D6
D7: JP1.8, R1.2, U$1.D7
D8: JP2.1, U$1.D8
D9: JP2.2, JP5.6, U$1.D9
D10: JP2.3, JP6.5, U$1.D10
D11: JP2.4, JP6.6, U$1.D11
D12: JP2.5, U$1.D12
D13: JP2.6, U$1.D13
GND: BUZZER6.-, C1.2, C2.2, C3.2, C4.2, C5.2, C6.2, IC1.1 (ADJ), J1.GND, J1.GNDBREAK, JP2.7, JP4.2, JP4.3, JP5.1, JP5.2, JP6.1, JP6.2, LED7.K (C), U$1.GND, U$1.GND1
unnamed: LED7.A, R1.1
unnamed: D1.A, J1.PWR
unnamed: BUZZER6.+, R2.1
RESET: JP4.6, U$1.RESET
RX: JP1.1, U$1.D0/RX
TX: JP1.2, U$1.D1/TX
VIN: C1.1, D1.C, IC1.3 (IN), JP4.1, U$1.VIN

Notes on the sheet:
Power Jack
Arduino Nano
4 Servos
Female Pin Headers
Programmable LED
Buzzer

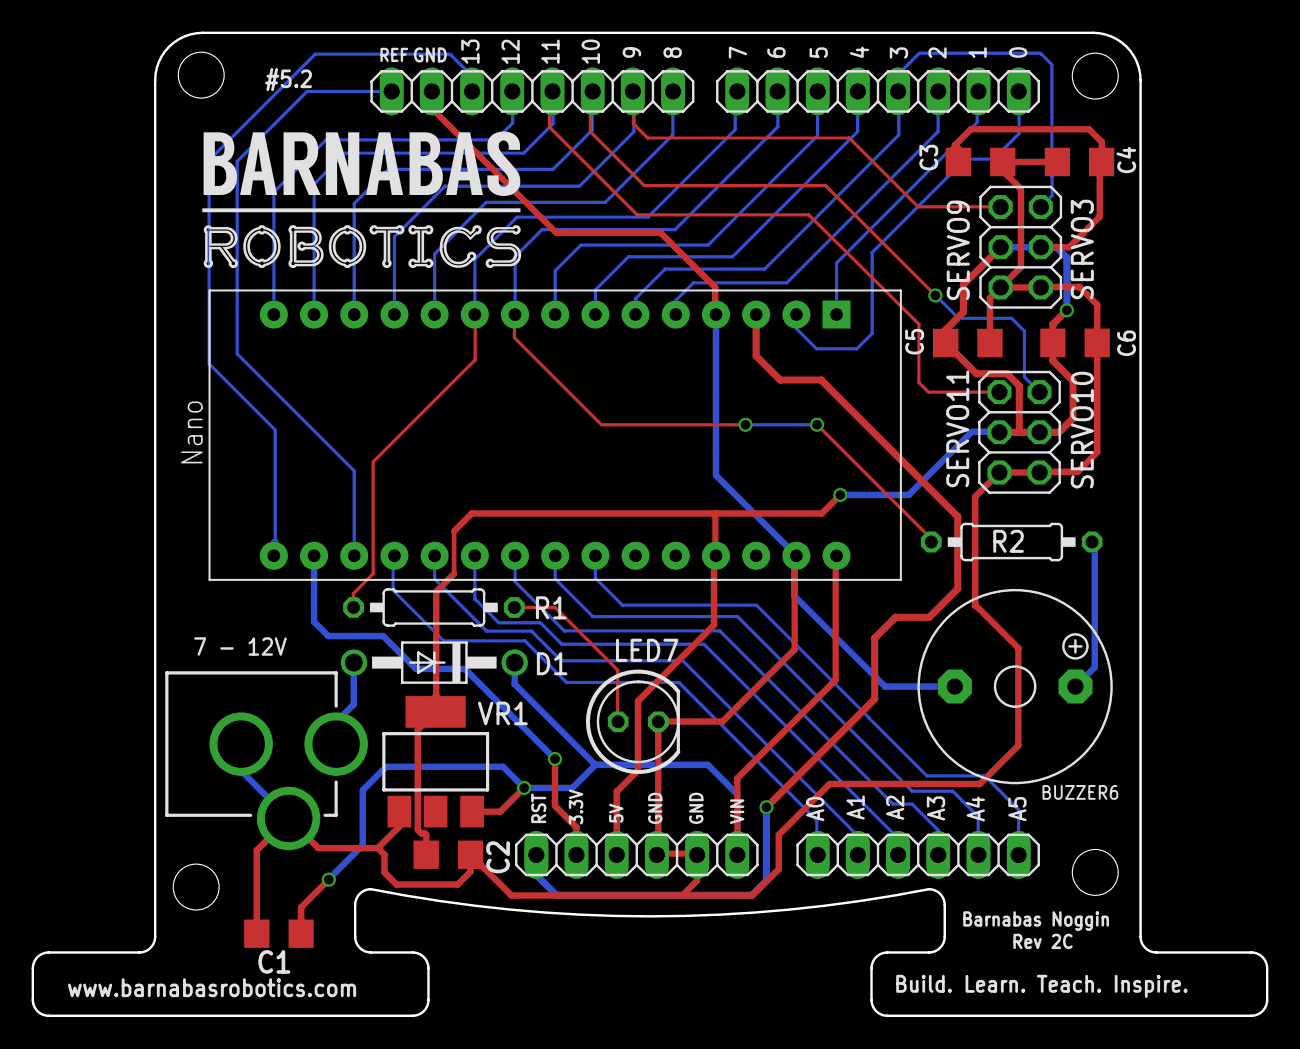
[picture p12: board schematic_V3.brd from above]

Board: 2 copper layers, 78.0 x 62.1 mm, 20 parts (0 on the bottom side), 29 nets.

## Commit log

2016-07-13 version two
    [schematic_V2.brd, schematic_V2.sch]
2016-07-13 Vincent added mounting holes
    [schematic_V2.brd]
2017-02-11 3rd revision of noggin - Vincent Kok
    Moved all components to top side of the board
2017-08-31 outline of pcb -- dxf files
2018-06-19 Add files via upload
    5VS and +5V rails merged
    [schematic_V2.brd, schematic_V2.sch]
2018-06-20 Rev C from Vincent
    [schematic_V3.brd, schematic_V3.sch]
2018-06-26 Add files via upload
    Connected 5VS and +5V rails. Minor cleanup of warnings prompted in Eagle
    [schematic_V3.brd, schematic_V3.sch]
2018-07-09 Thickened +5V traces
    [schematic_V3.brd]
2018-07-09 Designated VR1 as NO PLACE
    [BOM_BN_REV2C_EXPLORER_20180709_prod.xlsx]
2018-07-12 Up to date ger/drill files
2018-07-22 silkscreen corrected. 2C displayed as version.
2018-07-23 Now displays rev_2C as version no.
    [schematic_V3.brd]
2019-07-31 Finished schematic for V4 board. Added corresponding library and part database. Board not routed yet.
    [BOM_BN_REV2C_EXPLORER_20180709_prod.xlsx, barnabas_noggin_V4.brd, barnabas_noggin_V4.sch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]
2019-08-08 Updated V4 schematics.
    [barnabas_noggin_V4.brd, barnabas_noggin_V4.sch]
2019-08-08 Added V4 board schematics.
2019-08-12 Added 3.3V regulator.
    [barnabas_noggin_V4.brd, barnabas_noggin_V4.sch]
2019-08-16 complete routing
    [barnabas_noggin_V4.brd, barnabas_noggin_V4.sch]
2019-08-19 Upload latest schematics.
2019-08-19 Update board surface text.
    [barnabas_noggin_V4.brd, barnabas_noggin_V4.sch]
2019-08-20 update documentation print.
    [barnabas_noggin_V4.brd, barnabas_noggin_V4.sch]
2019-08-23 Modify silkscreen text. Update logo pattern.
    [barnabas_noggin_V4.brd, barnabas_noggin_V4.sch, barnabas_noggin_parts_db.csv]
2019-08-23 Update documentation print and schematics. Upload BOM file.
    [BOM_BN_REV3A_Explorer_20190823_prod.xlsx]
2019-08-23 modify logo and dc driver package.
    [barnabas_noggin_V4.brd]
2019-08-23 modify text.
    [barnabas_noggin_V4.brd]
2019-08-23 update board and schematics files.
    [barnabas_noggin_V4.brd, barnabas_noggin_V4.sch]
2019-11-08 Replaced with new ATMEGA328 chip and modified PWM pins
    [BOM_BN_REV3A_Explorer_20190823_prod.xlsx, barnabas_noggin_V4.brd, barnabas_noggin_V4.sch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]
2019-11-15 Replaced fuses. Added pull-up resistor for pin 2.
    [barnabas_noggin_V4.brd, barnabas_noggin_V4.sch]
2019-12-26 Fixed some silk screen text.
    [barnabas_noggin_V4.brd, barnabas_noggin_V4_ListByValues.xlsx]
2019-12-27 Uploaded new schematic PDF, documentation print, silkscreen from OSH, BOM and gerbers.
    [BOM_BN_REV3A_Explorer_20190823_prod.xlsx, BOM_BN_REV3A_Explorer_20191227_prod.xlsx, barnabas_noggin_V4.brd]
2020-01-16 Removed pin2 pullup resistor. Uploaded and updated files for Rev3B.
    [BOM_BN_REV3B_Explorer_20200116_prod.xlsx, barnabas_noggin_V4.brd, barnabas_noggin_V4.sch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]
2020-05-07 Modified V3 Board as new V3.1 Board and readme file
    [schematic_V3.1.brd, schematic_V3.1.sch]
2020-05-15 Finished routing and change the logo
    [schematic_V3.1.brd, schematic_V3.1.sch]
2020-05-18 Moved the logo and generated BOM
    [BOM_BN_REV2D_EXPLORER_20200518_prod.xlsx, barnabas_noggin_REV2D_ListByValues.xlsx, schematic_V3.1.brd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]
2020-05-26 autodesk files
    [barnabas_noggin_V4.brd, barnabas_noggin_V4.sch, barnabas_noggin_parts_db.csv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]
2020-06-08 modified the screensilk
    [schematic_V3.1.brd]
2020-06-08 change 4.7K resistor to 470 resistor
    [BOM_BN_REV2D_EXPLORER_20200518_prod.xlsx, BOM_BN_REV2D_EXPLORER_20200608_prod.xlsx, schematic_V3.1.brd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]
2020-06-10 Tried out assigning 3D models
    [schematic_V3.1.brd, schematic_V3.1.sch]
2020-06-11 Assigned more 3D models
    [schematic_V3.1.brd, schematic_V3.1.sch]
2020-06-11 Update library for V4 board
    [barnabas_noggin_V4.brd, barnabas_noggin_V4.sch]
2020-06-15 Updated Rev2D to Rev2E. Fixed screensilk and uploaded new BOM and gerbers
    [BOM_BN_REV2E_EXPLORER_20200611_prod.xlsx, schematic_V3.1.brd]
2020-06-30 Replace 3D models for resistors, LED, and Buzzer
    [barnabas_noggin_Rev2E.step, schematic_V3.1.brd, schematic_V3.1.sch]
